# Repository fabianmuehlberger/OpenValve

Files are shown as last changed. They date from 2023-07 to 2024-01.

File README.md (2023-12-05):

# OpenValve
open source smarthome radiator thermostat

<p align="center">
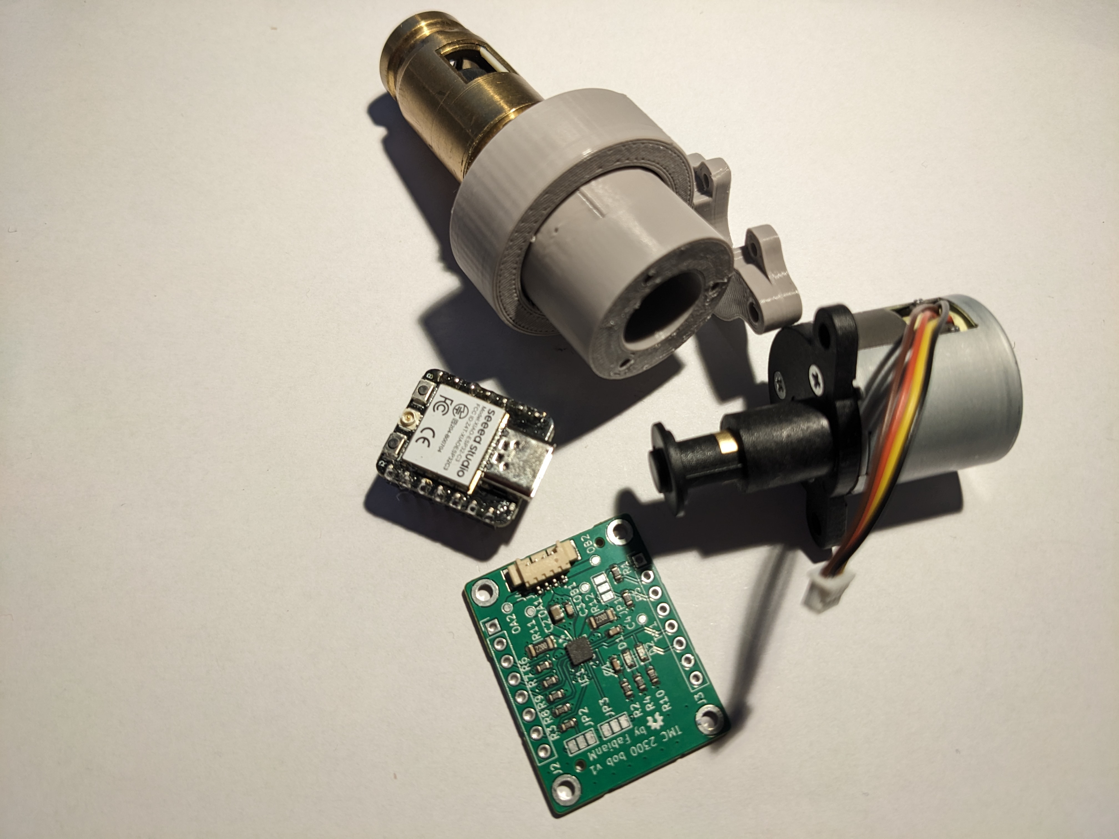
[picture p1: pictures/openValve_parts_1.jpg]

</p>

This project has the goal of developing an open source smarthome valve for radiators. 

## IDEA
* Using “off the shelf” components and 3D printed parts for easy building 
* keep  the cost at a minimum 
* allow programming via common environments (ESP-IDF, ESPHome) 
* integration into smarthome with ESPHome and Home Assistant

##  COMPONENTS
* Linear Stepper Motor for smart radiator valve
* 3D printed parts
* PCB 
  * ESP32 based board (esp32-c6 or esp32-c3)
  * stepper driver TMC 2300 
  * Battery management/ voltage regulator

## Mechanical design
The general idea is to make the mechanical Assembly and the program as simple as possible, to make it accessible and easy to work with. This is the premise for all design decisions   

<p align="center">
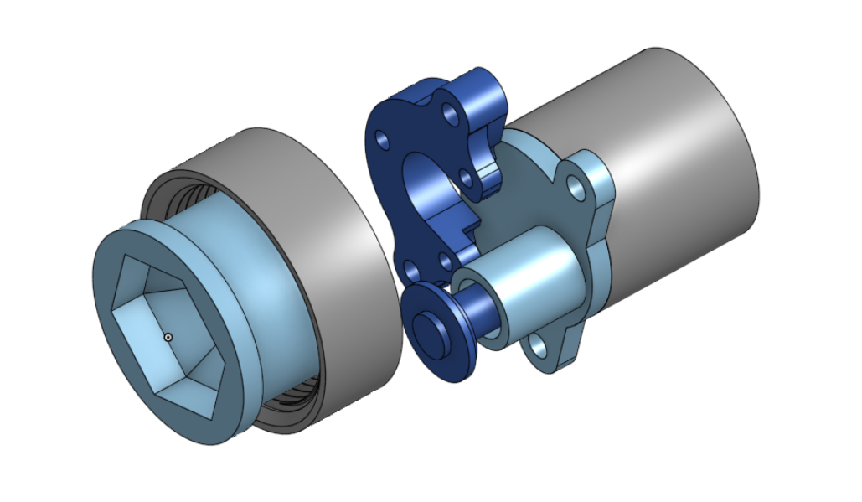
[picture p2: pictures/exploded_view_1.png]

</p>

### Radiator Valve 
<p align="center">
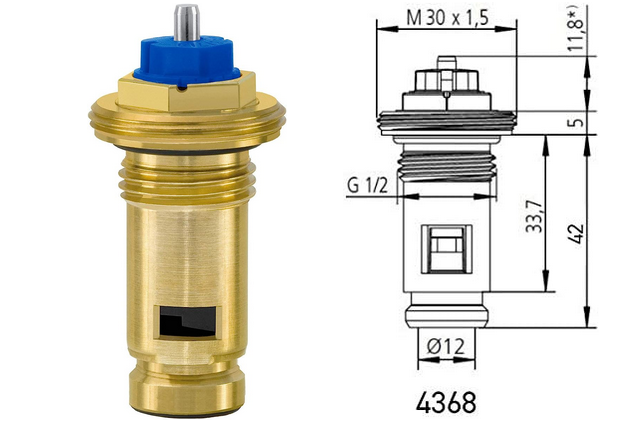
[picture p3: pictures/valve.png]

</p>

(standard radiator valve, used in Austria)
this sort of valve has a pin with ~2.5mmm travel, this allows for a controlled liquid flow depending on the distance. 
To make the SmartValve adjustable, a mechanism is needed to control the pin in that region. 

### Motor / Drive
The current development uses a geared stepper motor with 10:1 ration and a linear travel of ~ 5mm. The stepper is designed for this application.

### 3D printed parts
OpenValve is designed to have 3d printed parts that are printable with a standard FTM printer with no supports and assembled with m3 bolts and buts.    

<p align="center">
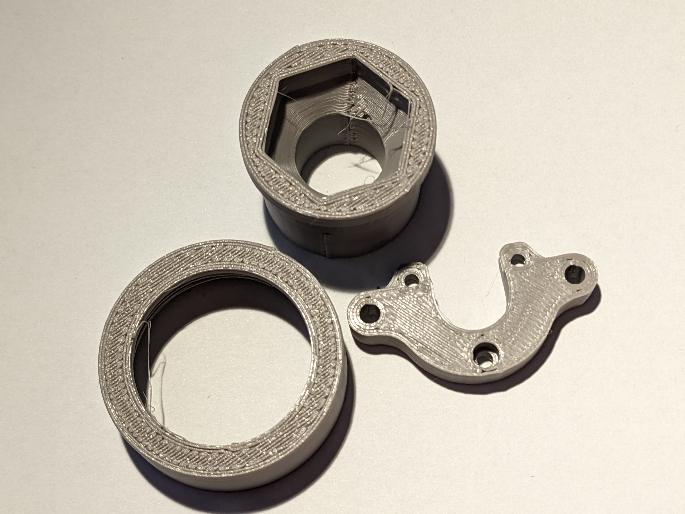
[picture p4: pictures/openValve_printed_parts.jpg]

</p>

[OnShape](https://cad.onshape.com/documents/391453e964c4cf36b71477fb/w/96218fe9ab75c37b541d1e8c/e/7027b69015998d7833889829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) is used for the projecrt for easy collaboration and versioning.

## SOFTWARE
* For easy integration in Home Assistant, the project is written in Arduino framework, this makes it possible to compile it as a ESPHome device

## TODO

### Prove of concept
- [x] 3D printed parts 
- [x] Arduino test sketch

### Prototype
- [ ] PCB design
  - [x] Schematic design
  - [x] Part selection for PCB
  - [x] PCB layout and Design
  - [x] PCB ordered
- [x] Prototype built
- [ ] Prototype tested
- [ ] prototype documentation

### Beta
- [ ] ESPHome code
- [ ] Home Assistant integration
- [ ] Durability test
- [ ] Beta documentation
- [ ] power consumption test

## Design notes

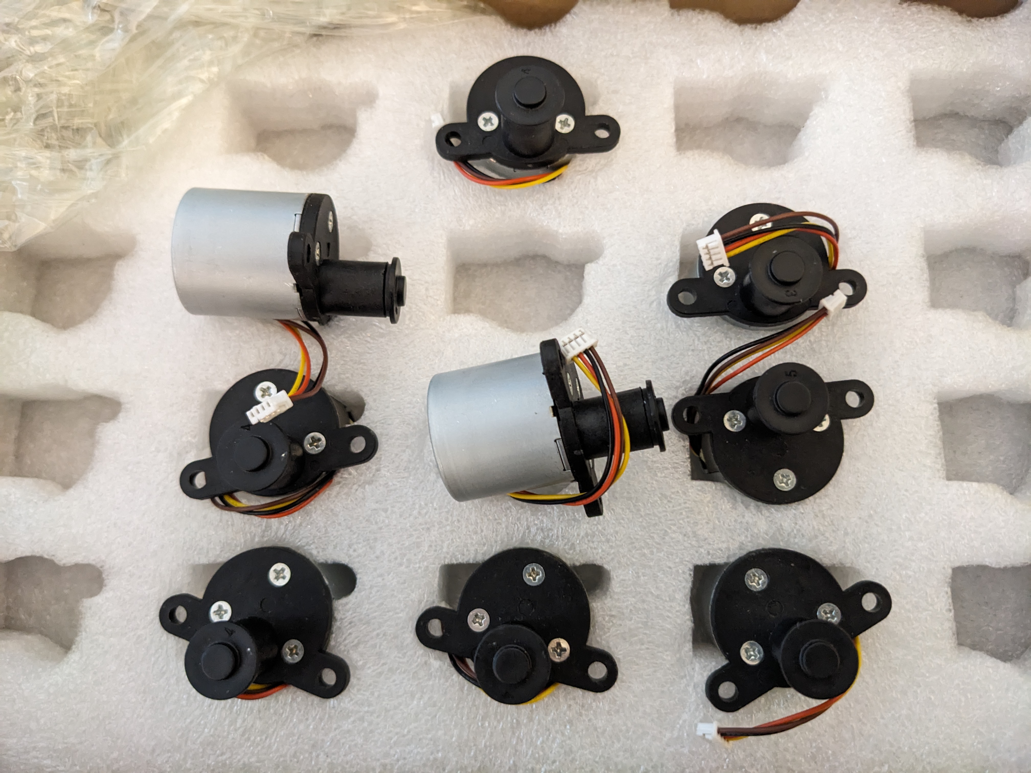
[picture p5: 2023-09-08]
pictures/openValve_delivery_1.jpg

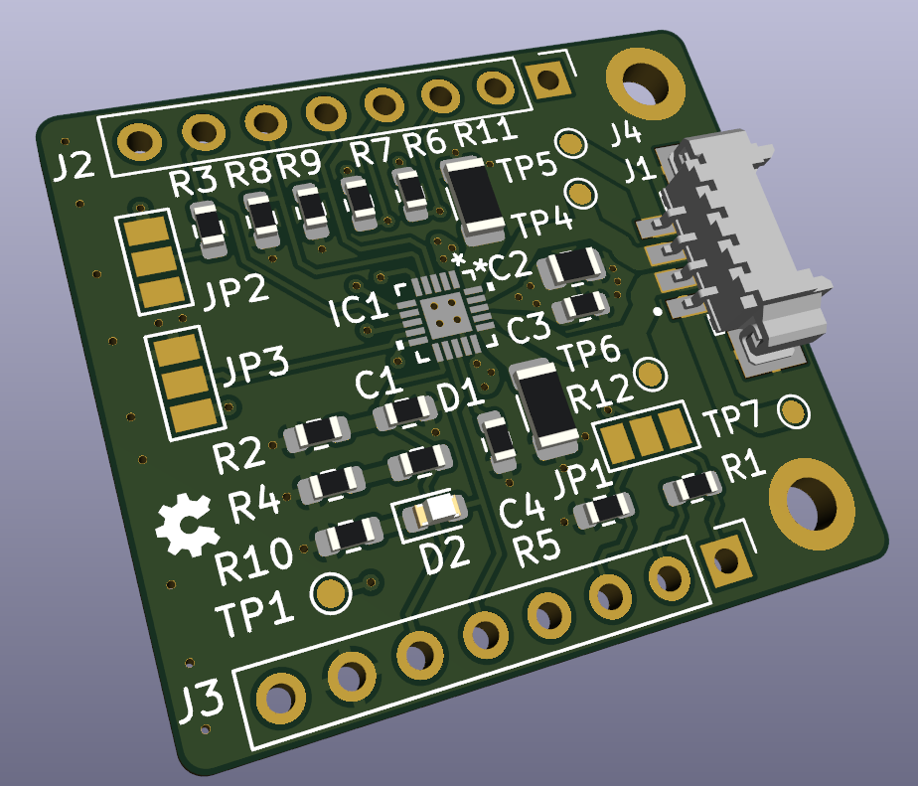
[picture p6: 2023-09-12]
pictures/tmc_2300_b0b_v1.png

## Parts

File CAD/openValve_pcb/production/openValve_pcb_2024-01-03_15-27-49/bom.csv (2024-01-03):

Designator | Footprint | Quantity | Value | LCSC Part #
C1, C3, C4 | 0603 | 3 | 100n
C2 | 0805 | 1 | 10u
D1 | 0603 | 1 | 0603/LED
D2 | 0603 | 1 | white/0603
H1, H2, H3, H4 | MountingHole_2.2mm_M2_DIN965_Pad | 4 | MountingHole_Pad
IC1 | QFN-20-1EP_3x3mm_P0.4mm_EP1.65x1.65mm_ThermalVias | 1 | TMC2300
J1 | PinHeader_1x04_P2.54mm_Vertical | 1 | Conn_01x04_Pin
J2 | PinHeader_1x07_P2.54mm_Vertical | 1 | Conn_01x07_Pin
J4 | PinHeader_1x07_P2.54mm_Vertical | 1 | Conn_01x08_Pin
J5 | PinHeader_1x03_P2.54mm_Vertical | 1 | Conn_01x03_Pin
R1, R2, R3, R6, R7, R8, R9 | 0603 | 7 | 100k
R10, R4 | 0603 | 2 | 1k
R11, R12 | 1206 | 2 | 220
U1 | MOUDLE14P-SMD-2.54-21X17.8MM | 1 | MOUDLE-SEEEDUINO-XIAO-ESP32C3

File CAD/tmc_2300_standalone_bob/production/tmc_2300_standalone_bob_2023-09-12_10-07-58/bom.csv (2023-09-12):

Designator | Footprint | Quantity | Value | LCSC Part #
C1, C3, C4 | 0603 | 3 | 100n
C2 | 0805 | 1 | 10u
D1 | 0603 | 1 | 0603/LED
D2 | 0603 | 1 | white/0603
IC1 | QFN20_3x3_TRI | 1 | TMC2300
J2, J3 | PinHeader_1x08_P2.54mm_Vertical | 2 | Conn_01x08_Pin
R1, R2, R3, R4, R5, R6, R7 | 0603 | 7 | 100k
R10, R9 | 1206 | 2 | 220
R8 | 0603 | 1 | 220

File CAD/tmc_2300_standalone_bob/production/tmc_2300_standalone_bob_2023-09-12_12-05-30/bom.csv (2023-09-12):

Designator | Footprint | Quantity | Value | LCSC Part #
C1, C3, C4 | 0603 | 3 | 100n
C2 | 0805 | 1 | 10u
D1 | 0603 | 1 | 0603/LED
D2 | 0603 | 1 | white/0603
IC1 | QFN20_3x3_TRI | 1 | TMC2300
J1 | PinHeader_1x04_P1.27mm_Vertical | 1 | Conn_01x04_Pin
J2, J3 | PinHeader_1x08_P2.54mm_Vertical | 2 | Conn_01x08_Pin
JP1, JP2, JP3 | SolderJumper-3_P1.3mm_Open_Pad1.0x1.5mm_NumberLabels | 3 | SolderJumper_3_Open
R1, R2, R3, R4, R5, R6, R7, R8, R9 | 0603 | 9 | 100k
R10 | 0603 | 1 | 220
R11, R12 | 1206 | 2 | 220
TP1, TP4, TP5, TP6, TP7 | TestPoint_Pad_D1.0mm | 5 | TestPoint

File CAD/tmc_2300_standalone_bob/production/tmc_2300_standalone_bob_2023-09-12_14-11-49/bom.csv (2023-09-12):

Designator | Footprint | Quantity | Value | LCSC Part #
C1, C3, C4 | 0603 | 3 | 100n
C2 | 0805 | 1 | 10u
D1 | 0603 | 1 | 0603/LED
D2 | 0603 | 1 | white/0603
DIAG, OA1, OA2, OB1, OB2 | TestPoint_Pad_D1.0mm | 5 | TestPoint
H1, H2 | MountingHole_2.2mm_M2_DIN965_Pad | 2 | MountingHole_Pad
IC1 | QFN20_3x3_TRI | 1 | TMC2300
J1 | PinHeader_1x04_P1.27mm_Vertical | 1 | Conn_01x04_Pin
J2, J3 | PinHeader_1x08_P2.54mm_Vertical | 2 | Conn_01x08_Pin
J4 | MOLEX_53261-0471 | 1 | 53261-0471
JP1, JP2, JP3 | SolderJumper-3_P1.3mm_Open_Pad1.0x1.5mm_NumberLabels | 3 | SolderJumper_3_Open
R1, R2, R3, R4, R5, R6, R7, R8, R9 | 0603 | 9 | 100k
R10 | 0603 | 1 | 220
R11, R12 | 1206 | 2 | 220

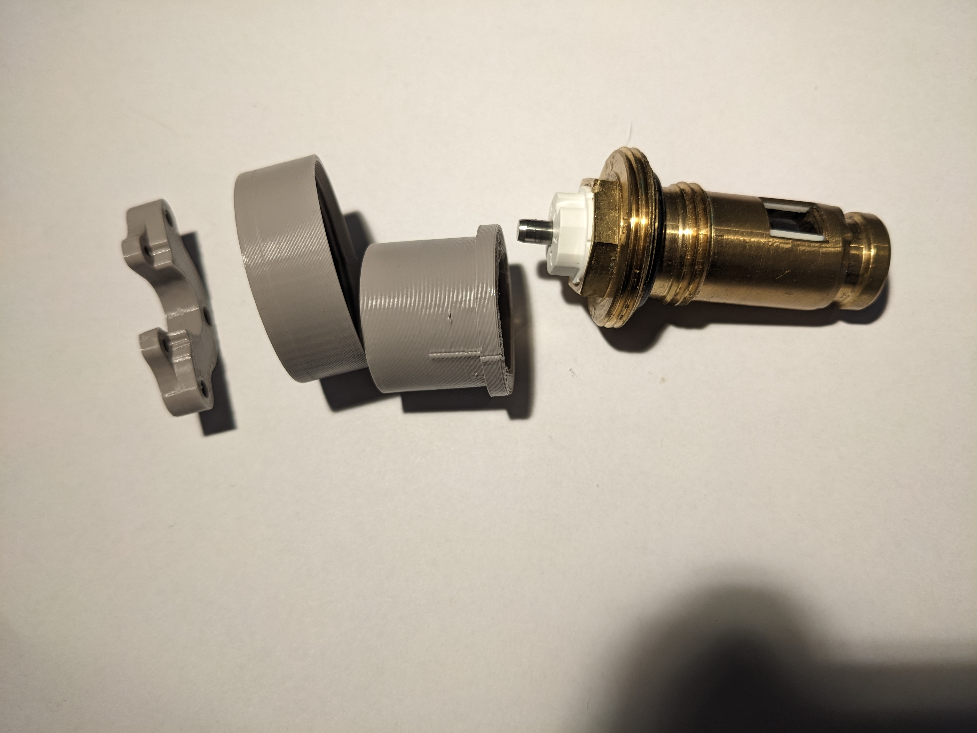
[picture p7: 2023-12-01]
pictures/openValve_parts_2.jpg

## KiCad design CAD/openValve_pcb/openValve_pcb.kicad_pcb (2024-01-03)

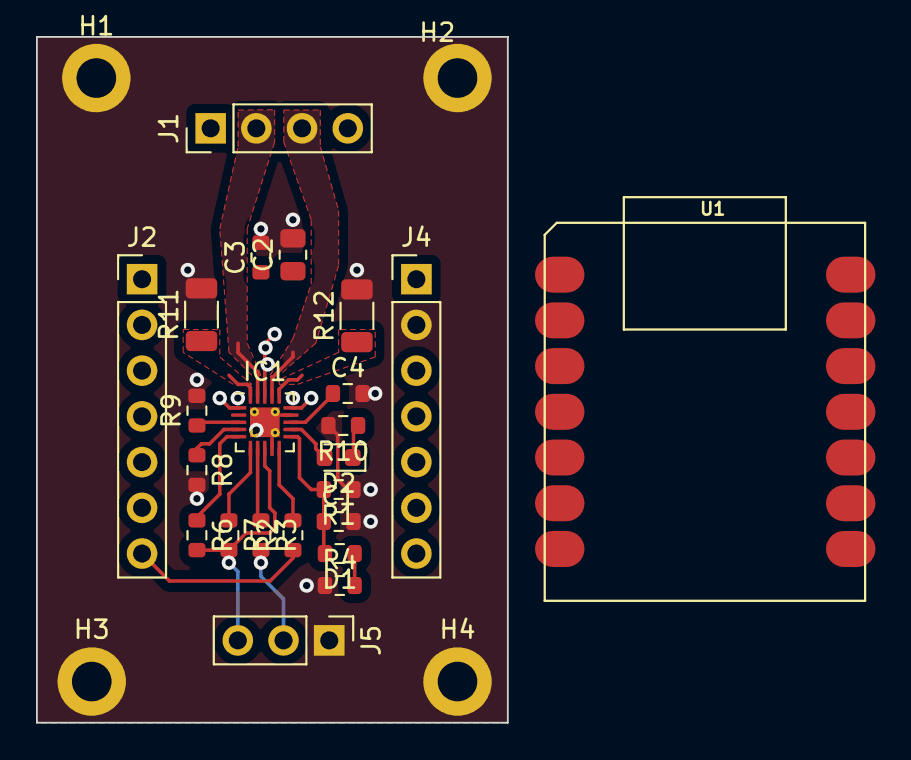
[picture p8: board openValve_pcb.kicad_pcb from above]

Board: 2 copper layers, 26.2 x 38.1 mm, 27 parts (0 on the bottom side), 22 nets.

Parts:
C1, C3, C4: 100n; R_0603_1608Metric
C2: 10u; R_0805_2012Metric
D1: 0603/LED; R_0603_1608Metric
D2: white/0603; LED_0603_1608Metric
H1, H2, H3, H4: MountingHole_Pad; MountingHole_2.2mm_M2_DIN965_Pad
IC1: TMC2300; QFN-20-1EP_3x3mm_P0.4mm_EP1.65x1.65mm_ThermalVias
J1: Conn_01x04_Pin; PinHeader_1x04_P2.54mm_Vertical
J2: Conn_01x07_Pin; PinHeader_1x07_P2.54mm_Vertical
J4: Conn_01x08_Pin; PinHeader_1x07_P2.54mm_Vertical
J5: Conn_01x03_Pin; PinHeader_1x03_P2.54mm_Vertical
R1, R2, R3, R6, R7, R8, R9: 100k; R_0603_1608Metric
R4, R10: 1k; R_0603_1608Metric
R11, R12: 220; R_1206_3216Metric
U1: MOUDLE-SEEEDUINO-XIAO-ESP32C3; MOUDLE14P-SMD-2.54-21X17.8MM

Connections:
+3.3V: C2.1, C3.1, IC1.8 (STEPPER), IC1.18 (VS), J4.3, J5.3, R6.2, R7.2, U1.12 (3V3)
+5V: J4.1, U1.14 (5V)
/DIAG: D2.2 (A), IC1.12 (DIAG), J2.2, U1.2 (PA4_A1_D1)
/DIR: IC1.3 (DIR), J2.4, R9.1, U1.4 (PA11_A3_D3)
/EN: IC1.7 (EN), J2.6, R3.1, U1.6 (PA9_A5_D5_SCL)
/MS1\AD0: IC1.5 (MS1/AD0), R6.1
/MS2\AD1: IC1.6 (MS2/AD1), R7.1
/OA1: IC1.19 (OA1), J1.2
/OA2: IC1.1 (OA2), J1.1
/OB1: IC1.17 (OB1), J1.3
/OB2: IC1.15 (OB2), J1.4
/PD/UART: IC1.10 (e~PD/UART), J4.7, R2.2, U1.8 (PB09_A7_D7_RX)
/SENS A: IC1.20 (BRA), R11.1
/SENS B: IC1.16 (BRB), R12.1
/STDBY: C1.1, D1.2 (A), IC1.11 (VIO/~STDBY), J2.3, R1.2, U1.3 (PA10_A2_D2)
/STEP: IC1.4 (STEP), J2.5, R8.1, U1.5 (PA8_A4_D4_SDA)
/TX: J2.7, R2.1, U1.7 (PB08_A6_D6_TX)
GND: C1.2, C2.2, C3.2, C4.2, H1.1, H2.1, H3.1, H4.1, IC1.9 (MODE), IC1.14 (GND), IC1.21 (PAD), J4.2, J5.1, R1.1, R4.1, R8.2, R9.2, R10.2, R11.2, R12.2, U1.13 (GND)
unnamed: D1.1 (K), R4.2
unnamed: D2.1 (K), R10.1
unnamed: C4.1, IC1.13 (1,8Vout)
unnamed: J5.2, R3.2

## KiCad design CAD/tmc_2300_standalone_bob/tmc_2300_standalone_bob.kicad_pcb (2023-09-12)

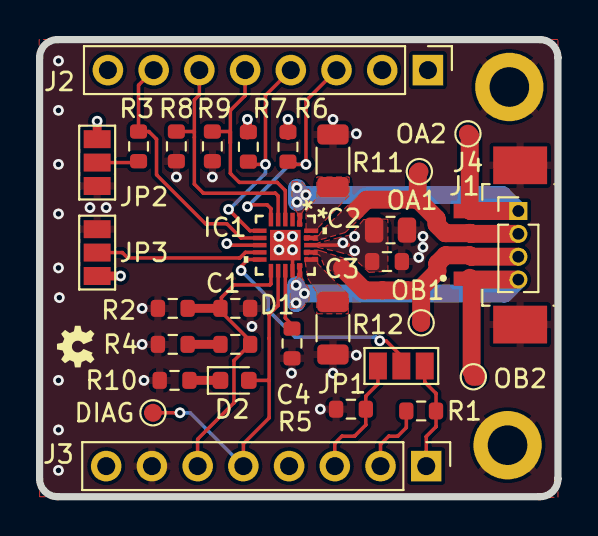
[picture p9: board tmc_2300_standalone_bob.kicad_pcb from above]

Board: 4 copper layers, 28.8 x 25.4 mm, 33 parts (0 on the bottom side), 24 nets.

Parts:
C1, C3, C4: 100n; R_0603_1608Metric
C2: 10u; R_0805_2012Metric
D1: 0603/LED; R_0603_1608Metric
D2: white/0603; LED_0603_1608Metric
DIAG: TestPoint; TestPoint_Pad_D1.0mm
H1, H2: MountingHole_Pad; MountingHole_2.2mm_M2_DIN965_Pad
IC1: TMC2300; QFN20_3x3_TRI
J1: Conn_01x04_Pin; PinHeader_1x04_P1.27mm_Vertical
J2, J3: Conn_01x08_Pin; PinHeader_1x08_P2.54mm_Vertical
J4: 53261-0471; MOLEX_53261-0471
JP1, JP2, JP3: SolderJumper_3_Open; SolderJumper-3_P1.3mm_Open_Pad1.0x1.5mm_NumberLabels
OA1, OA2: TestPoint; TestPoint_Pad_D1.0mm
OB1, OB2: TestPoint; TestPoint_Pad_D1.0mm
R1, R2, R3, R4, R5, R6, R7, R8, R9: 100k; R_0603_1608Metric
R10: 220; R_0603_1608Metric
R11, R12: 220; R_1206_3216Metric

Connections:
+3.3V: C2.1, C3.1, IC1.8 (STEPPER), IC1.18 (VS), J2.8, JP2.1 (A), JP3.3 (B), R6.2, R7.2
/DIAG: D2.2 (A), DIAG.1, IC1.12 (DIAG), J3.5
/DIR: IC1.3 (DIR), J2.5, R9.1
/EN: IC1.7 (EN), J2.7, R3.1
/MODE: IC1.9 (MODE), JP3.2 (C)
/MS1\AD0: IC1.5 (MS1/AD0), J2.3, R6.1
/MS2\AD1: IC1.6 (MS2/AD1), J2.4, R7.1
/OA1: IC1.19 (OA1), J1.2, J4.3, OA1.1
/OA2: IC1.1 (OA2), J1.1, J4.4, OA2.1
/OB1: IC1.17 (OB1), J1.3, J4.2, OB1.1
/OB2: IC1.15 (OB2), J1.4, J4.1, OB2.1
/PD: J3.3, JP1.1 (A), R5.2
/PD/UART: IC1.10 (e~PD/UART), JP1.2 (C)
/RX: J3.1, JP1.3 (B), R1.2
/SENS A: IC1.20 (BRA), R11.1
/SENS B: IC1.16 (BRB), R12.1
/STDBY: C1.1, D1.2 (A), IC1.11 (VIO/~STDBY), J3.6, R2.2
/STEP: IC1.4 (STEP), J2.6, R8.1
/TX: J3.2, R1.1
GND: C1.2, C2.2, C3.2, C4.2, H1.1, H2.1, IC1.14 (GND), IC1.21 (PAD), J3.7, J4.SH1 (SHIELD), J4.SH2 (SHIELD), JP2.3 (B), JP3.1 (A), R2.1, R4.1, R5.1, R8.2, R9.2, R10.2, R11.2, R12.2
unnamed: D1.1 (K), R4.2
unnamed: D2.1 (K), R10.1
unnamed: C4.1, IC1.13 (1,8Vout)
unnamed: JP2.2 (C), R3.2

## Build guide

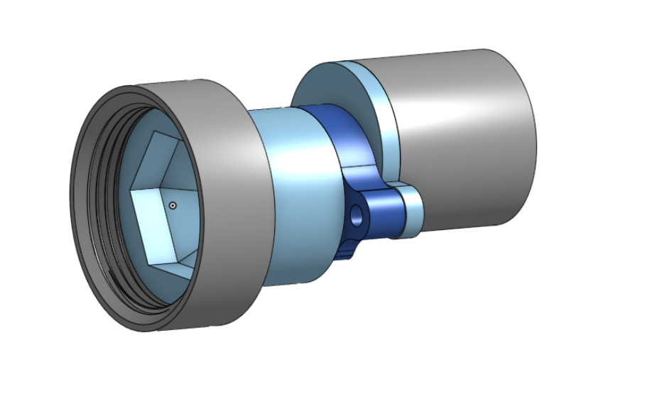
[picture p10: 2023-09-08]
pictures/assembled_1.png

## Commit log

2023-07-26 Add files via upload
    upload of 3D model
    [OpenValve v30_2023-07-26.step]
2023-07-29 updated code, added photo of prototype
2023-09-08 changed to prototype version 2
2023-09-08 added gitignore, removed old step files
    [OpenValve v30_2023-07-26.step]
2023-09-12 tmc2300 bob
    added custom bob for the tmc2300 driver to fit the lilygo t-oi MCU
    [bom.csv, designators.csv, positions.csv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]
2024-01-03 created xiao compatible board
    [bom.csv, designators.csv, openValve_pcb.kicad_pcb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]
